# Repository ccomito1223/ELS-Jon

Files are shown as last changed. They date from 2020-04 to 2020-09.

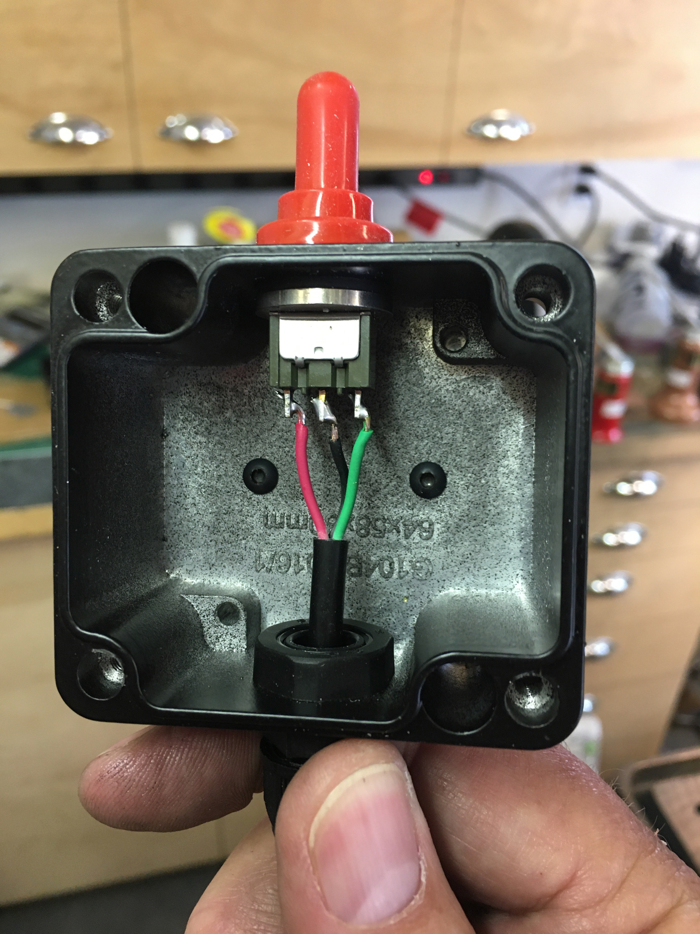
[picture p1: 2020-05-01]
Photos/Direction Switch Wiring.jpg

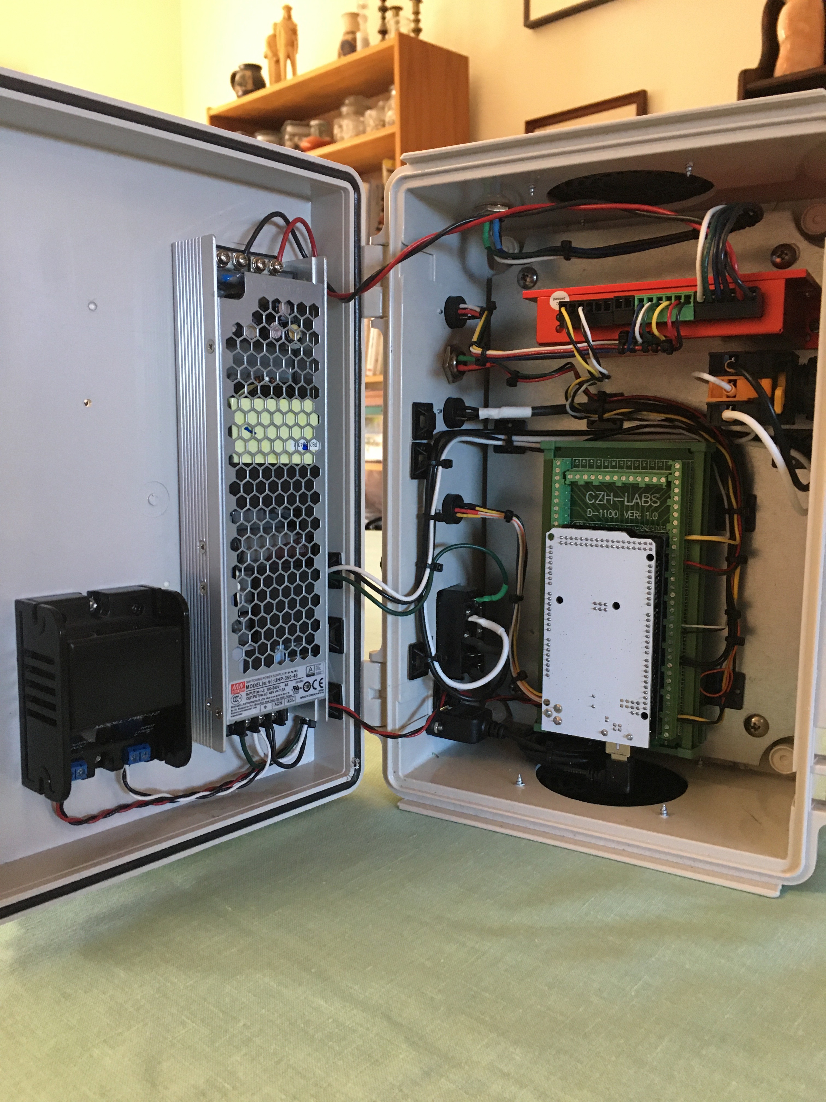
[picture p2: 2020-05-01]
Photos/CL57Y Build.jpg

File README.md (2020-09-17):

# ELS-Jon
Electronic Lead Screw - By  Jon Bryan

IMPORTANT USER NOTICE:
Always reprogram both the Arduino and Nextion together to avoid compatibility issues!

This repository is an attempt to document the development and implementation of a microcontroller-
based Electronic Lead Screw specifically intended for a 1946 Logan Model 200 lathe, but the
fundamental design principles have much broader potential applications.

The goal was to implement a design that would provide the user with a nearly-unlimited selection
of inch and metric thread pitches and feeds and obviate the need for change gears, while requiring
limited or no permanent modifications to the lathe.

The resulting system is based on an Arduino Mega 2560 microcontroller, an incremental rotary encoder
for sensing the position of the lathe spindle, and a closed-loop microstepping motor/driver to precisely 
drive the lathe lead screw at the desired rate relative to the rotation of the lathe spindle.

The user interface is provided by a Nextion NX4024K032 3.2" touch screen liquid crystal display, 
a 20 pulse-per-revolution encoder knob, and an optional single-pole, double-throw momentary toggle
switch for a conveniently-located alternative control of feed direction.

An attempt was made to implement every pitch available on a standard Logan lathe quick-change gearbox,
every inch and metric tap and die size available from McMaster-Carr up to 4tpi and 6.5mm, and
every legible pitch shown in photographs of the feed plates on lathes found through internet searches,
as well as a large selection of diametral and module worm gear pitches.  The maximum rates were limited 
for practical reasons, both because the Logan Model 200 is a relatively light-duty lathe and because of
the stall torque limit of the microstepping motor/driver.

Version 1.0 Features:

Inch feeds and threads from 0.0005" to 0.250" (4tpi)

Metric from 0.01mm to 6.5mm (including standard 0-10 British Association pitches)

Inch Diametral worm gear pitches from 120 to 12

Metric Module worm gear pitches from 0.2 to 2

Programmable left and right feed limits

A manual jogging function for precise positioning of the programmed limits

Display of the lathe spindle RPM

Display of the highest recommended lathe spindle RPM for a selected feed rate

Please visit and subscribe @ https://www.youtube.com/channel/UCw5ORyB1lIvQSxHoaDNEYuA

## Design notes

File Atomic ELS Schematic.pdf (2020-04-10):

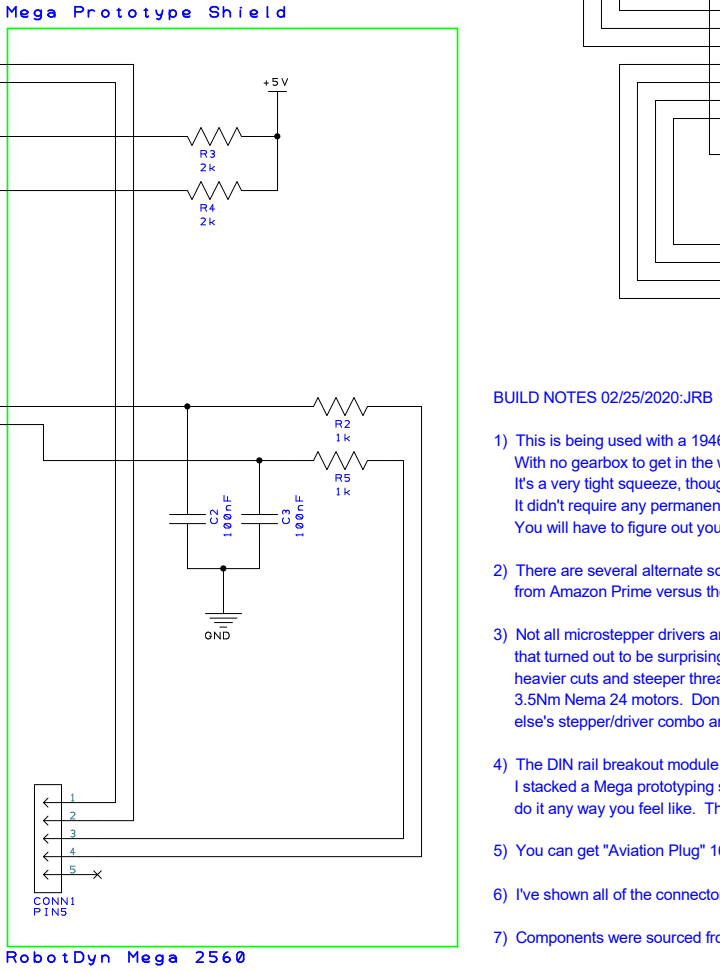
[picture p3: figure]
BUILD NOTES 02/25/2020:JRB

1) This is being used with a 1946 Logan Model 200 lathe. It was their entry-level model without a gearbox. With no gearbox to get in the way It just happens to make it ideal for a project like this.
It's a very tight squeeze, though. My Nema 24 motor fits with less than a millimeter to spare.
It didn't require any permanent modifications to my lathe, but that may not be the case for your installation. You will have to figure out your own mounting scheme if you use another lathe.
2) There are several alternate sources for the "Arduino" Mega. I use one from Elegoo that costs less than $19
from Amazon Prime versus the Genuine Arduino that is $45.
3) Not all microstepper drivers and motors are created equal. When I started this project I picked up a kit from Banggood that turned out to be surprisingly well-behaved. but I eventually decided that I really needed more torque to better handle heavier cuts and steeper threads, and I am currently using a CL57Y driver from OMC-Stepperonline with one of their 3.5Nm Nema 24 motors. Don't use the CL57T driver. It cogs pretty badly at low speeds. Use somebody
else's stepper/driver combo and all bets are off. The challenge is getting it all to fit.
4) The DIN rail breakout module allows the wire connections to be made with screw terminals.
I stacked a Mega prototyping shield on top of that for the pull-up resistors and RC filters, but you can
do it any way you feel like. This is fairly neat way to get it done short of a custom PCB.
5) You can get "Aviation Plug" 16mm connectors with from 2 to 10 pins, cheap. But use whatever connectors you like.
6) I've shown all of the connectors as 16mm "Aviation" style. Metal is cheap, sealed plastic not so much.
7) Components were sourced from Amazon, eBay and Digi-Key.

Yes, I know this switch is redundant. But it's what I had. Feel free to get a power entry module without a switch. Or don't use one.

I use a short USB panel mount pigtail to take this to the the side of my enclosure.

I'm using this particular power supply for several reasons. First, it's very compact for the power rating
Second, 48 volts provides somewhat higher torque.
Third, 350 watts provides a comfortable margin.
You could get away less power and a larger size to save money. Don't go below 36 volts and 240 watts, though.

DESIGNED AND BUILT BY JON BRYAN, EDGEWOOD, NEW MEXICO, USA. DRAWN MOSTLY AS-BUILT WITH ADVANCED CIRCUITS' PCB ARTIST.

THIS FITS IN A BUD NBF-32016 ABS ENCLOSURE.

## THE POWER SUPPLY AND AC DC CONVERTER ARE MOUNTED INSIDE OF THE LID, AND THE

REST IS MOUNTED ON AN NBX-32908 STEEL PANEL. BOTH WERE PURCHASED FROM AMAZON.
IT'S A PRETTY TIGHT SQUEEZE.

Metal 16mm "Aviation' connectors are cheap and come from 2 to 10 pins, Sealed plastic ones are expensive and have fewer selections for number of pins.

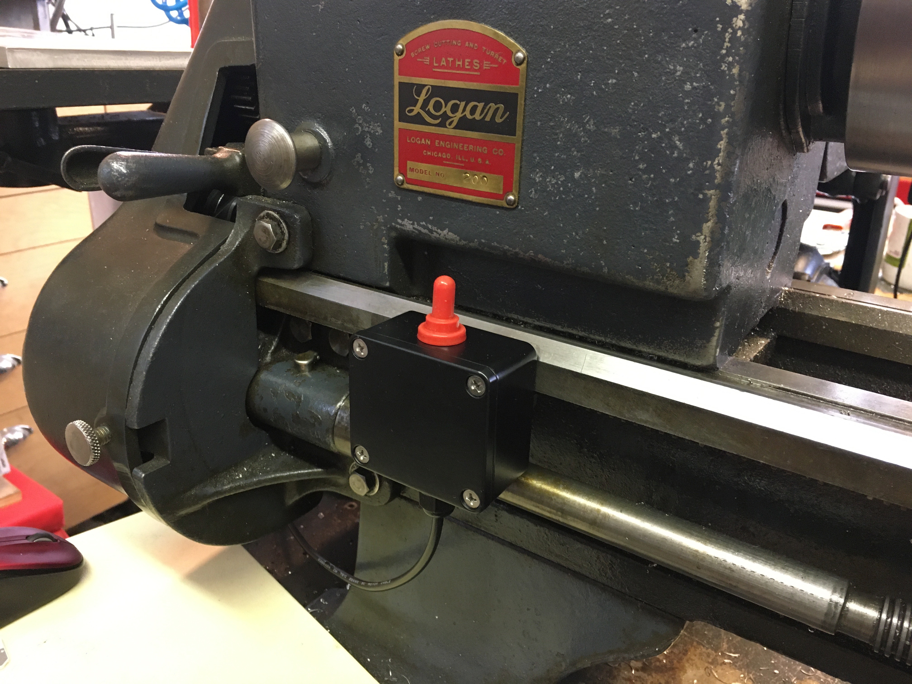
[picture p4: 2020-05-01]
Photos/Switch Enclosure Mounted.jpg

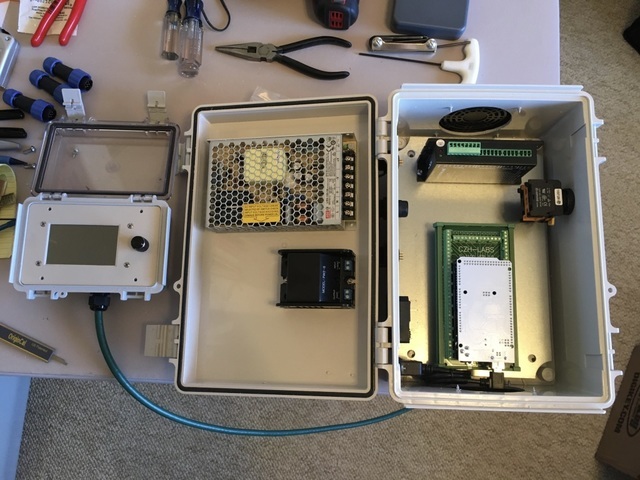
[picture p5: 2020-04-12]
Photos/qjOuRAnST4efVbV5aWy9EQ_thumb_1112.jpg

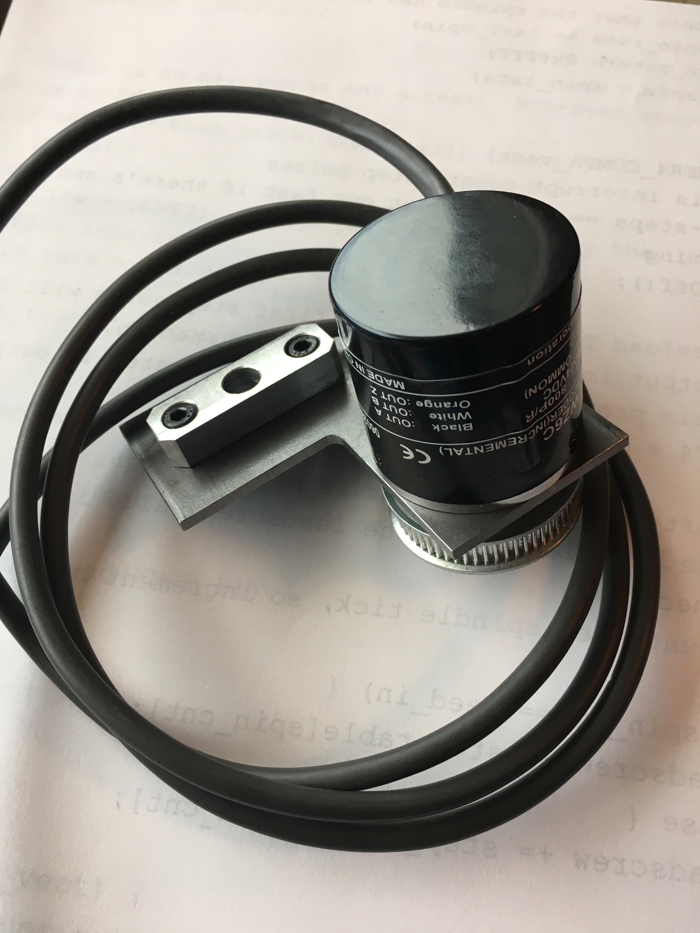
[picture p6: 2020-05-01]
Photos/Encoder Bracket.jpg

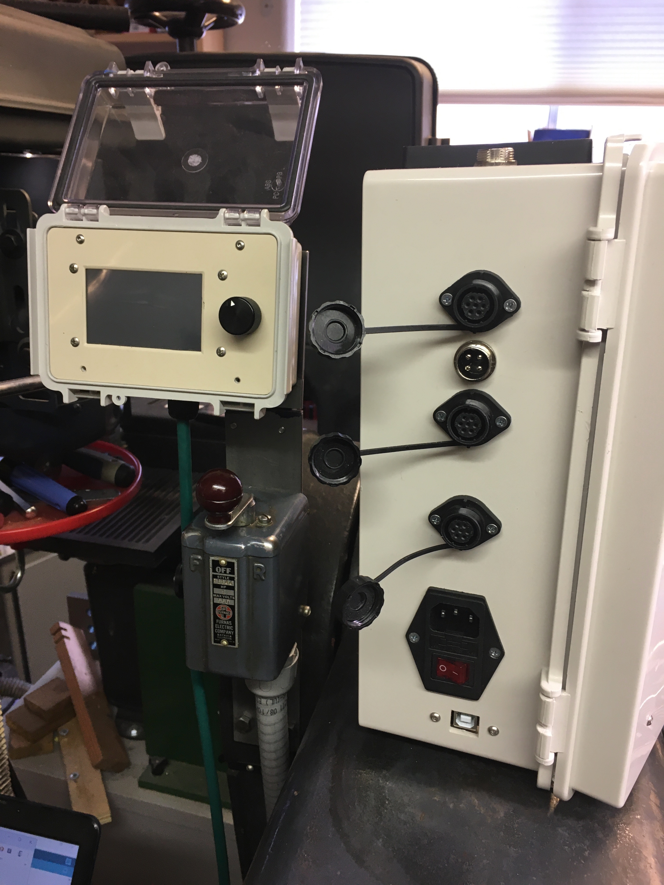
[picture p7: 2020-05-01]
Photos/Connectors.jpg

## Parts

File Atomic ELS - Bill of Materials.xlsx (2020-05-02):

QTY | Item | Description | Link | Cost | Notes
1 | Enclosure | Bud NBF-32016 plastic enclosure | https://www.amazon.com/gp/product/B005UPANU2/ref=ppx_yo_dt_b_search_asin_title?ie=UTF8&psc=1 | $27.91 | Main enclosure. It's tight, so you may want to shop around for something a bit larger.
1 | Steel Internal Panel | Bud NBX-32908 internal mounting panel | https://www.amazon.com/gp/product/B005UPERKY/ref=ppx_yo_dt_b_search_asin_title?ie=UTF8&psc=1 | $20.39 | Mounting panel for the enclosure. I find it a lot easier to mount everything on a panel before installing it in the enclosure.
1 | Enclosure | Bud NBF-32404 clear-lidded enclosure | https://www.amazon.com/BUD-Industries-NBF-32404-Plastic-Outdoor/dp/B005UPC0TE?s=industrial | $26.11 | Clear-lidded enclosure for the Nextion touchscreen display so that I could seal it all up if necessary. You can choose another enclosure if you don't want a lid, but I like having the option to seal it up. I drilled the corner screw holes of the Bud box through and screwed it down to a plate that I could hold in my mill vise, then milled a recess for the panel around the inside top edge flush with the inside edge of the gasket ridge. If you don't do that then you won't be able to close the lid. Climb cutting with a sharp end mill will result in a cleaner edge.
1 | Panel Brackets | Bud NBX-10930 panel brackets | https://www.digikey.com/products/en?keywords=NBX-10930 | $3.10 | Bud molds small dovetail slots into the inner walls of the NBF-32404 enclosure for these brackets. After cutting the inside rabbet to bring the front panel down flush I trimmed the tabs on these brackets and glued them in, then tapped them for 4-40 button head screws.
1 | Enclosure | Bud AN-1301-AB enclosure | https://www.amazon.com/gp/product/B06XCW5NVV/ref=ppx_yo_dt_b_search_asin_title?ie=UTF8&psc=1 | $12.84 | Small enclosure for the direction-select toggle switch that I attach magnetically to the ways in front of the headstock.
8 | Channel Magnets | Neodymium bar magnets in steel channels | https://www.amazon.com/gp/product/B078KJSSJG/ref=ppx_yo_dt_b_search_asin_title?ie=UTF8&psc=1 | $17.99 | The channel concentrates the magnetic field and increases the holding power so that they hold very securely. I mounted a short length of cold-rolled bar to the enclosure, then mounted these on the bar to stick to the under side of the ways. One of the photos on GitHub shows it. If it's not secure enough for you, use two.
8 | Encoder | KY-040 Rotary Encoder Module with knob | https://www.amazon.com/WGCD-KY-040-Degree-Encoder-Arduino/dp/B07B68H6R8?s=electronics | $12.99 | Cheap 20p/r rotary encoder(s). I didn't like the small knob, so I replaced it with a bigger one. Depending on the knob you use, you may have to trim the encoder shaft to fit the knob closer to the panel and have enough clearance to close the lid.
1 | Stepper Driver Kit Option 1 | Closed loop Stepper Kit 495.74 oz.in Nema 24 Closed loop Stepping Driver | https://www.ebay.com/itm/1-Axis-Closed-loop-Stepper-Kit-495-74-oz-in-Nema-24-Closed-loop-Stepping-Driver/333327613415 | $96.30 | The kit seems to be the only way to get this motor now, and it will probably be unobtainium soon. This is the one that I have installed, but the CL57T driver cogged badly at low speed and provided inconsistent torque at stall. The motor has a 25mm long 8mm shaft, and Nema 23-compatible mounting holes. It's really unfortunate that Stepperonline has replaced this with a motor that has a 10mm shaft, less torque, is a few millimeters longer, and has different spacing on the mounting holes.
1 | Stepper Driver Kit Option 2 | YE Series 1 Axis Closed Loop Stepper CNC Kit 3.0 Nm (424.92oz.in) Nema 24 Motor & Driver | https://www.omc-stepperonline.com/closed-loop-stepper-kit/ye-series-1-axis-closed-loop-stepper-cnc-kit-3-0-nm-424-92oz-in-nema-24-motor-and-driver.html | $91.15 | This kit comes with the CL57Y driver, which I highly recommend. Stepperonline says that it is “optimized for balanced performance” where the CL57T is aimed more at high-speed applications. It's quiet and generates consistent low-speed torque. The motor, however, is a big problem. It has a 10mm shaft, and it's a few millimeters longer than the 3.5Nm motor that I'm using. I needed every single millimeter to fit the motor in the available space. So I recommend buying the preceding kit for the 3.5Nm motor and buying the CL57Y driver separately. Sorry.
1 | Recommended stepper driver | Y Series Closed Loop Stepper Driver 0-7.0A 24-50VDC for Nema 17, 23, 24 Stepper Motor | https://www.omc-stepperonline.com/closed-loop-stepper-driver/y-series-closed-loop-stepper-driver-0-7-0a-24-50vdc-for-nema-17-23-24-stepper-motor.html | $44.82 | This driver is working great for me. It growls a little bit at very low speeds, but quickly smooths out and generates much more consistent torque at stall than the CL57T, which also cogs really badly at low speeds.
1 | 800PPR Encoder | OMRON 800P Incremental Rotary Encoder 800p/r 5-24v DC E6B2-CWZ6C NPN | https://www.ebay.com/itm/NEW-1PC-OMRON-800P-Incremental-Rotary-Encoder-800p-r-5-24v-DC-E6B2-CWZ6C-NPN/303247814222 | $22.50 | 800p/r E6B2-CWZ6C open-collector rotary encoder to keep track of the spindle. That gives me a resolution of ~39 microinches per step with the microstepper set to 400 steps per revolution. The bracket tucks it in under the reversing lever. I add 2k pull-up resistors at the Arduino inputs because the Arduino's internal pull-ups are more like 20k and make the rising edges too slow. You could buy the -CWZ3E voltage output version instead, which has the 2k resistors built in, but I like to think that I get a little better noise immunity with them right at the Arduino inputs.
1 | Arduino Mega | ATmega2560 | https://www.amazon.com/ELEGOO-ATmega2560-ATMEGA16U2-Projects-Compliant/dp/B01H4ZLZLQ | $16.98 | Half the price of Genuino, works great for me
1 | Nextion Display | Nextion 3.2 Inch TFT LCD Touch Screen with 16MB Flash | https://www.amazon.com/gp/product/B01LAG13DA/ref=ppx_yo_dt_b_search_asin_title?ie=UTF8&psc=1 | $34.99 | These do all the display and touchscreen work for you, and all you need is a serial port to talk to them. You have to use their editor to design the display layout.
1 | Alternate Breakout Board | Arduino Mega Terminal Board | https://www.amazon.com/Electronics-Salon-Terminal-Breakout-Arduino-MEGA-2560/dp/B07H9TJCWN?s=industrial | $32.00 | Expensive, but more compact than the DIN rail board
1 | MD-D1100T-1 Breakout Board | Arduino Mega DIN Rail Terminal Board | https://www.amazon.com/gp/product/B01CU3OB5Y/ref=ppx_yo_dt_b_search_asin_title?ie=UTF8&psc=1 | $35.00 | Expensive, but makes for a neat install
1 | UHP-350-48 Power Supply | Meanwell Slim Power Supply - 350W 48V 7.3A | https://www.ebay.com/itm/POWERNEX-MEAN-WELL-NEW-UHP-350-UHP-350R-350W-Slim-PFC-Switching-Power-Supply/254313542946 | $75.00 | Expensive, but fits in my enclosure. You can use a larger, less expensive supply if you can work out how to make it fit, or have a larger enclosure. I was running with a 36V supply for a long time, but 48V provides more torque, and it's still quiet with the CL57Y driver
1 | USB extension cable | Left-angled Type B male to female | https://www.amazon.com/gp/product/B00S5WJ5RO/ref=ppx_yo_dt_b_search_asin_title?ie=UTF8&psc=1 | $4.99 | I brought the Arduino USB to the outside of the enclosure with this because there wasn't enough clearance left to plug into the Arduino directly. Depending on how you mount your Arduino, you may need a right-angled version.
 | USB Type B Female Dust Plug | Silicone plug to keep FOD out of the receptacle | https://www.amazon.com/gp/product/B00XP4E0LI/ref=ppx_od_dt_b_asin_title_s01?ie=UTF8&psc=1 | $3.64 | Always a good idea to keep crud out of your connectors.
1 | PFL-22 Illuminated Pushbutton Switch | Alpinetech 22mm push-on/push-off power switch with 110V LED | https://www.amazon.com/gp/product/B00FLZ6ZYE/ref=ppx_yo_dt_b_search_asin_title?ie=UTF8&th=1 | $13.95 | I really like Alpinetech's 22mm switches, but they come with one NO and one NC contact block.
1 | NO Contact Block | Alpinetech Normally Open contact block | https://www.amazon.com/Alpinetech-Normally-Open-Contact-Block/dp/B00IJ4FIZ6?s=industrial | $4.95 | Pull the NC block from the switch and replace it with this. Or only switch one AC leg. I guess I'm a belt-and-suspenders kind of guy.
1 | Fused Power Entry | Male power cord socket with fuse holder | https://www.amazon.com/dp/B071H7X2XG (https://www.amazon.com/dp/B071H7X2XG?spLa=ZW5jcnlwdGVkUXVhbGl) | $6.89 | The schematic shows a switched power entry because that's what I had. You don't need the switch, but you had better have the fuse.
1 | Power Supply | Power Supply Cord for Arduino | https://www.amazon.com/yan-Power-Supply-Arduino-Elegoo/dp/B07PF2X8CV?s=industrial | $10.99 | Basic wall wart
1 | Molex 1554216010 Multiconductor cable | 8-conductor 24AWG cable | https://www.digikey.com/product-detail/en/molex/1554216010/WM15680-1-ND/8321936 | $10.61 | Cable to connect the Nextion display and encoder knob to the Arduino. This happens to be Ethernet-rated twisted pairs, but that isn't required or even necessarily desirable. You just need enough wires to carry the signals. I wouldn't go any larger than 24 gauge though, or the cable will get too large and stiff.
1 | C-TON PW2-12 AC/DC Converter | 1 Watt 115VAC/12VDC Converter | https://www.digikey.com/product-detail/en/c-ton-industries/PW2-12/CDPM1001-ND/371487 | $15.68 | I'm using this converter to power the Arduino and, indirectly, the Nextion display, rotary encoder knob and spindle encoder, and have it mounted inside the main enclosure where it is powered from the AC line in parallel with the 48V supply.
 | Cable Glands, PG7, PG9, PG11, PG13.5, PG16 | Hilitchi 30pc Cable Gland Assortment | https://www.amazon.com/gp/product/B01MDTUIIA/ref=ppx_yo_dt_b_search_asin_title?ie=UTF8&psc=1 | $9.99 | Waterproof stress relief for the cabling. The kit is overkill, but you're not really going to save much money going some other way. I used one gland for the direction toggle switch enclosure, and one for the display enclosure. You could also use connectors. I may be moving the direction toggle switch lines to the Nextion I/O to simplify the programming, in which case that cable will move from the main enclosure to the display and I will most likely add an “Aviation plug” jack to the Nextion enclosure.
 | GX16-7 Connector Sets | “Aviation” plug sets, 16mm 7-pin | https://www.amazon.com/uxcell-Aviation-Connector-Waterproof-Fittings/dp/B07DC7STLJ?s=hi | $12.99 | These so-called “Aviation Plug” sets are commonly used in home-brew CNC setups, and are probably the least-expensive (i.e. kind of chintzy) connectors that you can use. They come with from 2 to 10 pins/sockets, and are easy to assemble if you don't try to use wire that's too big for the solder pots. If you want to upgrade, use the sealed plastic versions.
 | GX16-4 Connector Sets | “Aviation” plug sets, 16mm 4-pin | https://www.amazon.com/dp/B01GA48SG2 (https://www.amazon.com/dp/B01GA48SG2?spLa=ZW5jcnlwdGVkUXVhbGl) | $14.99 | This is the 4-pin connector that the Stepperonline motors come with. For this and the preceding 7-pin connector, there are lots of suppliers, so shop around.
1 | 120T-B8 15T | 8:1 120T/15T HTD3M timing pulley setup with a 15mm belt to drive the leadscrew | https://www.ebay.com/itm/HTD3M-120T-B8-15T-Timing-Pulley-Belt-Width-15mm-Set-Kit-Reduction-Ratio-8-1-CNC/142416259123 | $49.99 | 8:1 ratio to drive the leadscrew, with a 15-tooth pulley on the motor. You can buy the sets for about $50. The 120-tooth pulley fits under the cover of a Logan Model 200, but there's no room to spare. In a pinch you could turn a couple of millimeters off the pulley flanges. Select the 8mm bore 15-tooth pulley and the 95.7mm "wheelbase". I have 3D printed timing pulleys ordered (04/10/2020) from Shapeways, and will let everyone know if they work out.
1 | HTD420-3M | 15mm wide timing belt | https://www.ebay.com/itm/HTD-3M-Closed-Rubber-Timing-Belt-Drive-Belt-225-486mm-Belt-10-15-20-25mm-Width/124123911598 | $2.59 | If you buy the pulleys separately, this 15mm belt should work for you (on a Logan lathe).
2 | GT2 60 | 60-tooth 2GT timing pulleys | https://www.ebay.com/itm/GT2-60T-Timing-Belt-Pulley-Bore-5-6-6-35-7-8-10-12-14-15mm-For-6-10mm-Width-Belt/163967005530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 | $8.89 | The encoder has a 6mm shaft, but the GT2 pulleys are hard to find with that bore. I just use one with a 5mm bore and ream it to 6mm. I turn the boss off of this one too, and relocate the setscrew. As mentioned in the previous item, 3D printed pulleys are on order, and if they work the cost is pretty reasonable.
0 | GT2 60 Model | GT2 6mm belt and pulleys for the spindle/encoder | https://comcast2877.autodesk360.com/g/shares/SH919a0QTf3c32634dcf1f01f9dbbc2bce0a |  | I had to break down and learn some Fusion 360 in order to create these models. I always had a full-time CAD jockey do this stuff before I retired, and the learning curve is a little steep, but worth the effort. Fusion 360 is an incredible (free) deal. I remember when Pro Engineer used to cost $100k for the “basic” package, another $20k if you wanted to do sheet metal, and about $20k a pop for each additional add-on. Fusion 360 will do a lot more than ProE could do back then.
0 | GT2 60 Model | GT2 6mm belt and pulleys for the spindle/encoder | https://comcast2877.autodesk360.com/g/shares/SH919a0QTf3c32634dcf639ea8194b7155bb |  | One has to be modified to fit the stud gear shaft, and the other has to have the boss turned off and then has to be re-drilled with the setscrew in the middle.
10 | 220-2GT-6 | 6mm Timing Belt | https://www.amazon.com/2GT-Timing-Belt-Closed-Loop/dp/B07GX9Q5SG | $16.99 | This size belt is working for me. Timing belts are incredibly strong. A little 6mm belt may not look impressive, but is probably rated for almost 300 pounds. Driving the encoder presents almost no load, so this belt ought to last for many years.
1 | Bracket 1 3D Model | Bracket for Nema23/24 Motor | https://comcast2877.autodesk360.com/g/shares/SH919a0QTf3c32634dcf06d520aa33e49140 |  | The 3.5Nm “Nema 24” motor that I'm currently using has the same 47.14mm mounting hole pattern as a Nema 23, but other “Nema 24” motors have a 50mm pattern. The Nema 24 motor frame is 60.3mm versus the Nema 23's 56.4mm. You will have to adjust this to work with whatever you wind up using.
1 | Bracket 1 2D Drawing | Bracket for Nema23/24 Motor | https://comcast2877.autodesk360.com/g/shares/SH919a0QTf3c32634dcfdacc95df96ec1bd0
1 | Bracket 2 3D Model | Bracket for Rotary Encoder | https://comcast2877.autodesk360.com/g/shares/SH919a0QTf3c32634dcf00f401d77292e1a6
1 | Bracket 2 2D Drawing | Bracket for Rotary Encoder | https://comcast2877.autodesk360.com/g/shares/SH919a0QTf3c32634dcf876f0e371c003be1
1 | 120T-B8 15T 3D Model | 3D model for modifications to 120T | https://comcast2877.autodesk360.com/g/shares/SH919a0QTf3c32634dcf97d8a990778473de
1 | 120T-B8 15T 2D Drawing | 3D model for modifications to 120T
1 | Faceplate 3D Model | 3D Model for Nextion Display | https://comcast2877.autodesk360.com/g/shares/SH919a0QTf3c32634dcf989d775cd617d30b
1 | Faceplate 2D Drawing | 2D drawing for Nextion Display | https://comcast2877.autodesk360.com/g/projects/20200322277515676/data/dXJuOmFkc2sud2lwcHJvZDpmcy5mb2xkZXI6Y28uVGJ3OUJKWEpRRFNkNmVRQW5CQ0o5dw/dXJuOmFkc2sud2lwc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
2 | Terminal Blocks | Dual Row 5 Position Screw Terminal Strip 600V | https://www.amazon.com/gp/product/B010UDG6NG/ref=ppx_yo_dt_b_search_asin_title?ie=UTF8&psc=1 | $10.91 | I happened to have some of these. You only need 4 terminals. I like terminal blocks because they make things neat.
1 | Toggle Switch | Sealed MOM/OFF/MOM SPDT Switch | https://www.digikey.com/product-detail/en/nkk-switches/M2018WBG01/360-3404-ND/6022016 | $18.03 | I went full belt-and-suspenders here, with a sealed switch and a boot as well.
1 | Toggle Switch Boot | Silicone rubber switch boot | https://www.digikey.com/product-detail/en/nkk-switches/AT402C/360-1707-ND/599026 | $5.78 | This one is red. I almost went with yellow. Or green. Your call.
1 | Friction Hinge | Southco E6-10-301-20 Series Adjustable Torque Position Control Hinge | https://www.amazon.com/gp/product/B00GM5G89E/ref=ppx_yo_dt_b_search_asin_image?ie=UTF8&psc=1 | $10.54 | I mounted the Nextion display enclosure on a hinged extension above the drum switch, which is mounted on a length of 2" x 3/16" hot-rolled flat bar bolted to the motor belt guard. This friction hinge allows me to adjust the angle to my liking.
 | Nextion Editor |  | https://nextion.tech/nextion-editor/#_section1
 | Arduino IDE |  | https://www.arduino.cc/en/main/OldSoftwareReleases
 | AtomicELS_V1.zip |  | https://github.com/ccomito1223/ELS-Jon |  | Contains two folders, one for the Arduino and one for the Nextion. Extract the Arduino folder to where you're putting your Arduino sketches, open the folder in the IDE, and load AtomicELS. You will get three tabs, AtomicELS, configuration.h and tables.h. Compile and upload to your Mega. Extract the AtomicELS.hmi file, load it into the Nextion Editor, select "File/TFT file output" from the drop-down menu, click on "Output" and save the AtomicELS.tft file to a MicroSD card. Plug the MicroSD card into your Nextion display and power it up, and it will program itself. Turn off the power, unplug the MicroSD card, and turn the power back on. You should see the ELS default display.
 | Atomic ELS Schematic.pdf |  | https://github.com/ccomito1223/ELS-Jon |  | Drawn with PCB Artist downloaded from 4pcb.com, which is a very capable free tool.

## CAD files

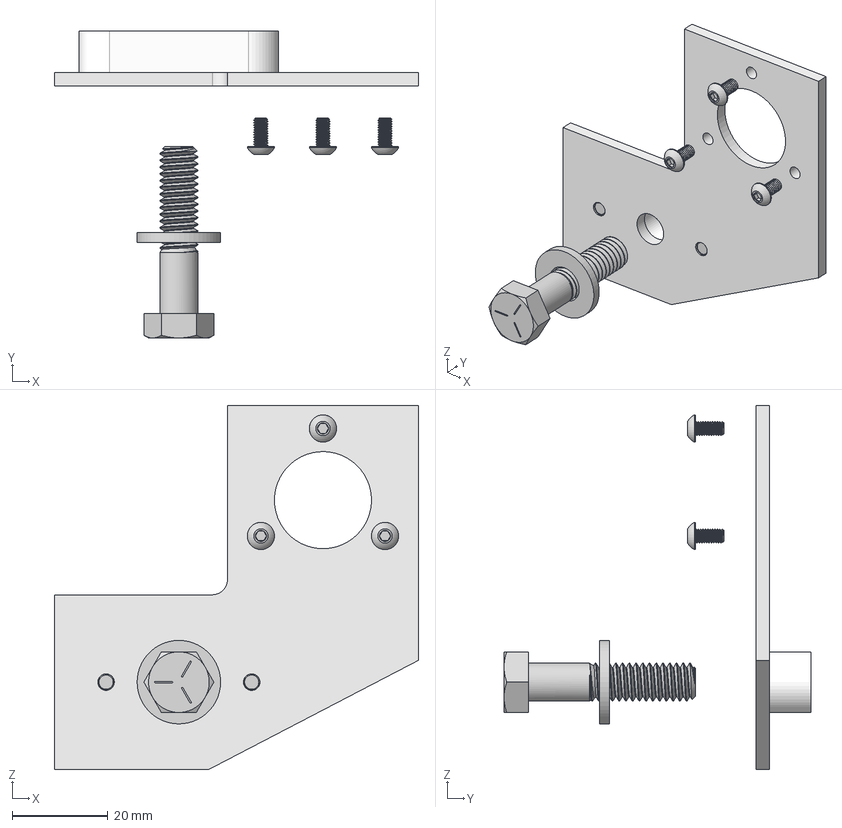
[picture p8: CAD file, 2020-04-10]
CAD/Logan Model 200 Encoder Bracket.stp
76.2 x 64.3 x 76.2 mm
Plate
Tang
91251A190 x 2
91239A111 x 3
90126A030
92865A158

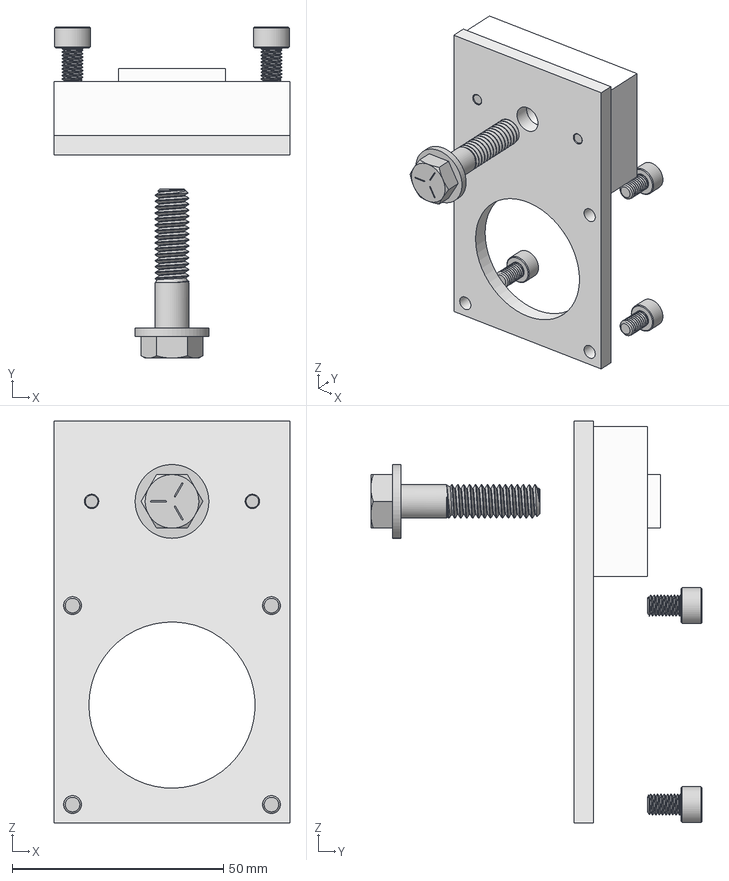
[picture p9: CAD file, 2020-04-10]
CAD/Logan Model 200 Motor Bracket.stp
55.9 x 78.5 x 95.2 mm
Plate
Spacer (1)
91251A192 (1) x 2
91290A222 x 4
92865A158
90126A030

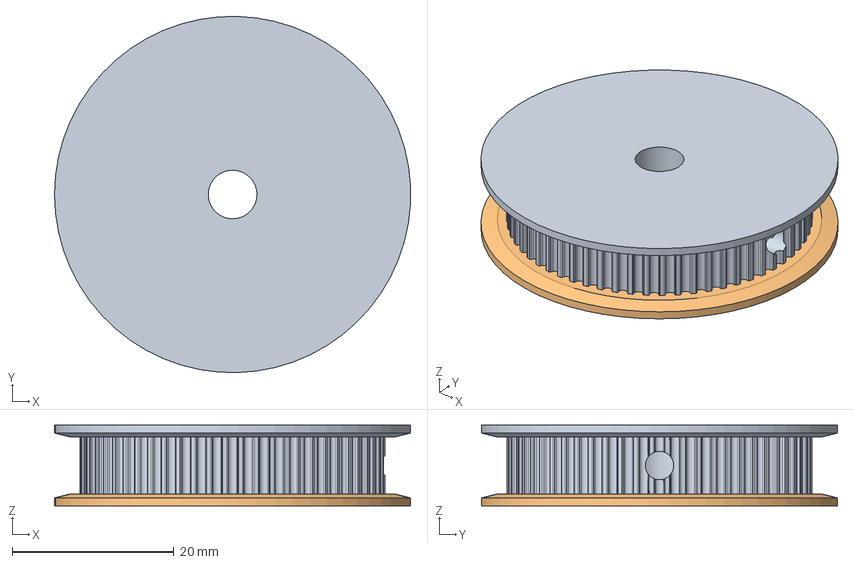
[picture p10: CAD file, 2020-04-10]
CAD/GT2 60T Timing Pulley 6mm Bore.stp
44.0 x 44.0 x 10.0 mm

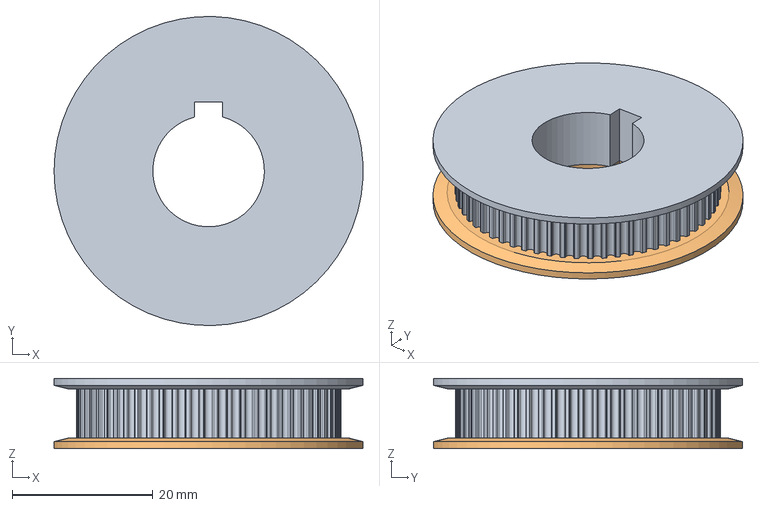
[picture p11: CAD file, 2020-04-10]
CAD/GT2 60T Timing Pulley 5_8_ Bore.stp
44.0 x 44.0 x 10.0 mm

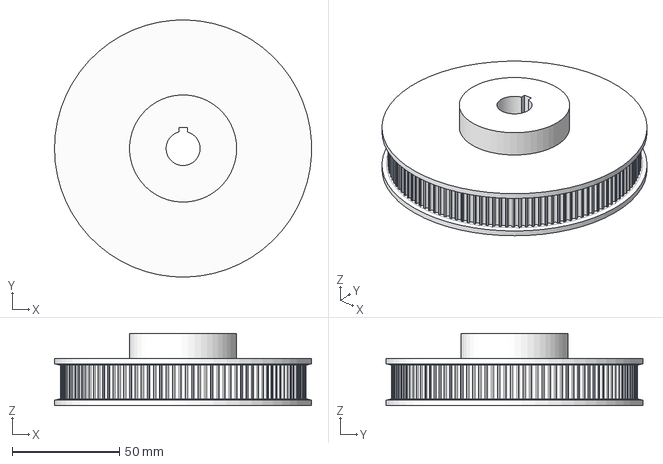
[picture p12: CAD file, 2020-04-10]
CAD/HTD3M 120T-B12 Timing Pulley.stp
119.9 x 120.0 x 33.7 mm

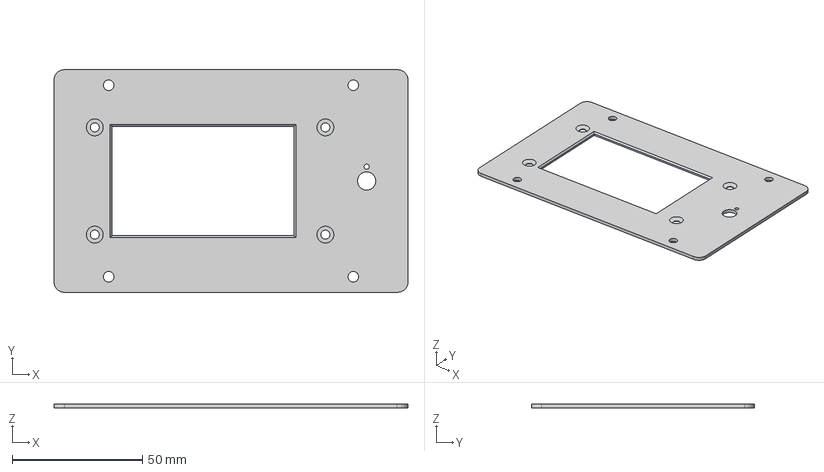
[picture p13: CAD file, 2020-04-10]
CAD/Nextion Faceplate.stp
136.0 x 85.5 x 1.59 mm

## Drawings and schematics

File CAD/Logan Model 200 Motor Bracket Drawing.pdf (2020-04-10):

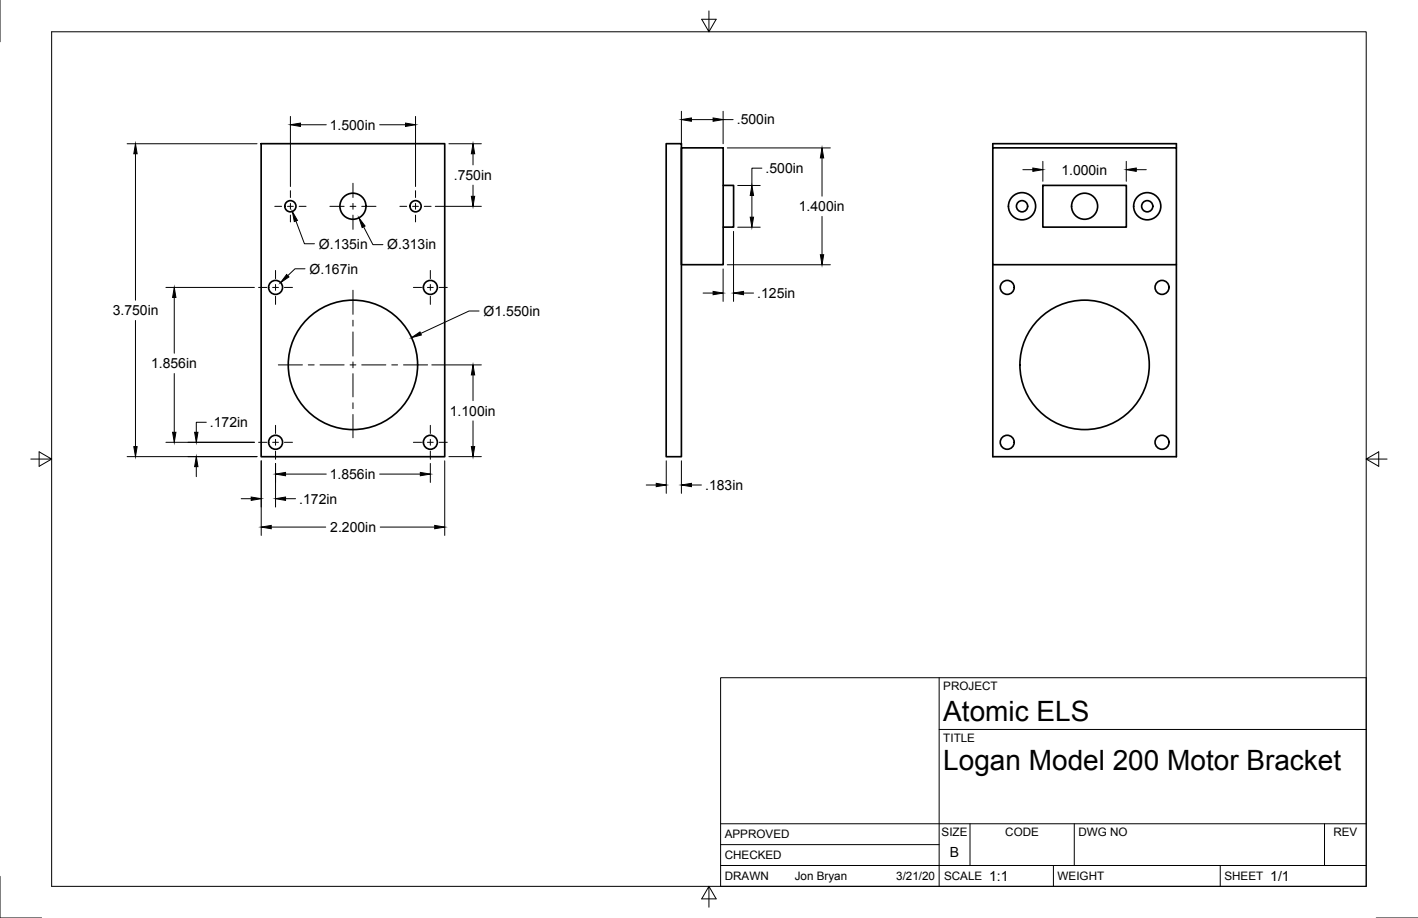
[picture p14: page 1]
SIZE; CODE; DWG NO; REV; Jon Bryan

PROJECT
Atomic ELS
Logan Model 200 Motor Bracket

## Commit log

2020-04-09 Add files via upload
    I'm assuming that you're using a Windows computer for your development system.
    After downloading and installing the Nextion Editor, unzip the Nextion file to your Nextion working directory and open the AtomicELS HMI file in the Editor. Click on "Debug" in the Editor and it shou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
    [ELS - Bill of Materials.xlsx]
2020-04-10 Delete ELS - Bill of Materials.xlsx
    Rev A added
    [ELS - Bill of Materials.xlsx]
2020-04-10 Add files via upload
    Added 3d Model
    [GT2 60T Timing Pulley 5_8_ Bore.stp, GT2 60T Timing Pulley 6mm Bore.stp, HTD3M 120T-B12 Timing Pulley.stp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]
2020-04-10 Delete ArduinoAtomicELS.zip
    Revised folder structure
2020-04-11 Add files via upload
    Revised parts list per Jon.
    [Atomic ELS - Bill of Materials Rev2.xls]
2020-04-11 Delete ELS - Bill of Materials Rev1.xlsx
    replaced per rev2
    [ELS - Bill of Materials Rev1.xlsx]
2020-04-12 Add files via upload
    Arduino. Download and unzip. This will extract properly and will compile. If you downloaded the original files from the forums and are having troubles, delete it and grab this one.
    [configuration.h]
2020-04-12 Add files via upload
    Photos showing general arrangement of pulley, motor and encoder.
2020-04-13 Add files via upload
    Showing the latest (04/13/2020) arrangement with the CL57Y driver and small form-factor 48V/350W power supply.
2020-04-23 Add files via upload
    Fixed synchronization bug in Arduino sketch, and implemented RPM blanking for the Nextion.
    Some small changes were made in the Nextion code, making the RPM text boxes global in scope and making a few small cosmetic adjustments.
    The Nextion display must be updated for this version of the Arduino code to work.
